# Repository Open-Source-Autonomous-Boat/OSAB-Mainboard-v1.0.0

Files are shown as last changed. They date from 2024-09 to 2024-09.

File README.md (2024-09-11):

# OSAB-Mainboard-v1.0.0
Mainboard for navigation and control of the vessel. Based on the RP2040. This is a prototype design that is not polished or suitable for use by others. It has been made freely available for educational and historical reasons only.

> ***NOTE:* V1.0.0 IS A PROTOTYPE VERSION. It is not recommended for ANY use. V1.0.0 is the only iteration in the V1.x.x series.**

### Features
- RP2040 processor (16MB flash)
- USB-C power and data connector
- SWD debugging port
- Boot select and reset button
- LiPo/Li-Ion backup battery with charger
- Red power indicator LED
- Yellow battery charge indicator LED
- Three blue LEDs (User-programmable, located in a line for optional use as a 3-bit binary status/error code output)
- Two WS2812B RGB LEDs (User-programmable)
- 4x DIP switch array for input (User-programmable)
- E-STOP button connector (JST-PH)
- Leak sensor connectors (two channels, two inputs per channel, JST-PH)
- GPS (PA1616D)
- CR1220 coin cell holder for GPS (retains sat. positions and speeds up reboot)
- LoRa (RFM95CW)
- Connector for Adafruit BNO085 accelerometer/gyro/magnetometer module (JST-SH)
- SD card slot for mission files and data logging
- PWM servo and ESC output (JST-PH)
- CAN-Bus and 12v input (JST-PH)
- MCP25625 CAN-Bus controller/transceiver
- Two MPM3610 buck converters (12v to 5v and 3.3v)
- AP2112K linear voltage regulator for USB input (5v to 3.3v)

### Notes
- LoRa and CAN-Bus controller share SPI1
- Mounting holes don't fit M3 screws, but should fit M2.5 or M2
- DOUBLE CHECK THAT YOUR LiPo/Li-Ion BATTERY HAS BEEN WIRED WITH THE CORRECT POLARITY BEFORE CONNECTING
- Changing the value of R6 sets the charging current for the backup battery (10k = 100mA, 5k = 200mA, 2k = 500mA, 1k = 1000mA)

### Known Issues
- I2C pullup resistors for the BNO085 connector are series resistors, not pullup resistors (oops)
- Diode on the boot select button serves no purpose (originally intended to allow the button to serve as a user-programmable button after bootup, but was not connected due to a lack of available GPIO)

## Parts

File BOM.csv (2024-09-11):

ID | Name | Designator | Footprint | Quantity | Manufacturer Part | Manufacturer | Supplier | Supplier Part | Price
1 | CR1220-2 | B1 | BAT-SMD_CR1220-2 | 1 | CR1220-2 | Q&J | LCSC | C70381 | 0.217
2 | 10uF | C1,C4,C18,C20,C23,C26,C33 | C0603 | 7 | CSA0603X5R106M6R3JT | HRE(芯声) | LCSC | C3015157 | 0.005
3 | 27pF | C2,C3,C28,C29 | C0402 | 4 | GJM1555C1H270JB01D | muRata(村田) | LCSC | C88884 | 0.014
4 | 100nF | C5,C6,C7,C9,C11,C12,C13,C14,C15,C16,C19,C21,C24,C25,C30 | C0402 | 15 | GCM155R71C104KA55D | muRata(村田) | LCSC | C85857 | 0.003
5 | 1uF | C8,C10 | C0402 | 2 | TCC0402X5R105K100AT | CCTC(三环) | LCSC | C380293 | 0.002
6 | 22uF | C22,C27 | C0603 | 2 | CL10A226MQ8NRNC | SAMSUNG(三星) | LCSC | C59461 | 0.008
7 | 47pF | C31,C32 | C0603 | 2 | CL10C470JB8NNNC | SAMSUNG(三星) | LCSC | C1671 | 0.004
8 | S2B-PH-SM4-TB(LF)(SN) | CN1,CN2,CN5,CN6,CN7,CN8 | CONN-SMD_P2.00_S2B-PH-SM4-TB-LF-SN | 6 | S2B-PH-SM4-TB(LF)(SN) | JST | LCSC | C295747 | 0.167
9 | PH2.0-3PWB Horizontal | CN3,CN4 | CONN-TH_PH-3PWB | 2 | PH-3P卧贴 | BOOMELE(博穆精密) | LCSC | C81626 | 0.064
10 | BM03B-SRSS-TBT(LF)(SN) | CN11 | CONN-SMD_BM03B-SRSS-TBT-LF-SN | 1 | BM03B-SRSS-TBT(LF)(SN) | JST | LCSC | C495538 | 0.279
11 | SM04B-SRSS-TB (LF)(SN) | CN12 | CONN-SMD_4P-P1.00_SM04B-SRSS-TB-LF-SN | 1 | SM04B-SRSS-TB(LF)(SN) | JST | LCSC | C160404 | 0.161
12 | MBR0540 | D1,D3,D4,D5,D6 | SOD-123FL_L2.7-W1.8-LS3.8-RD | 5 | MBR0540 | SHIKUES(时科) | LCSC | C116159 | 0.017
13 | NSR0320MW2T1G | D2 | SOD-323_L1.8-W1.3-LS2.5-RD | 1 | NSR0320MW2T1G | onsemi(安森美) | LCSC | C48192 | 0.052
14 | HL-PSC-2012U36FC | LED1,LED8 | LED0805-RD_RED | 2 | HL-PSC-2012U36FC | HONGLITRONIC(鸿利光电) | LCSC | C497949 | 0.076
15 | E6C0805UYAC1UDA | LED2 | LED0805-R-RD | 1 | E6C0805UYAC1UDA | ekinglux(亿晶源) | LCSC | C375452 | 0.02
16 | HL-PC-2012H392BC-L | LED3,LED4,LED5 | LED0805-RD_BLUE | 3 | HL-PC-2012H392BC-L | HONGLITRONIC(鸿利光电) | LCSC | C497943 | 0.014
17 | WS2812B-B/W | LED6,LED7 | LED-SMD_4P-L5.0-W5.0-TL_WS2812B-B | 2 | WS2812B-B/T | worldsemi | LCSC | C2761795 | 0.076
18 | DMP2045U-7 | Q1 | SOT-23-3_L2.9-W1.3-P1.90-LS2.4-BR-CW | 1 | DMP2045U-7 | DIODES(美台) | LCSC | C459541 | 0.078
19 | 1kΩ | R1,R5,R16,R17,R26 | R0603 | 5 | 0603WAF1001T5E | UNI-ROYAL(厚声) | LCSC | C21190 | 0.001
20 | 10kΩ | R2,R10,R11,R13,R14,R15,R20,R21,R29,R30,R31 | R0603 | 11 | FRC0603F1002TS | FOJAN(富捷) | LCSC | C2906982 | 0.001
21 | 27Ω | R3,R4 | R0402 | 2 | 0402WGJ0270TCE | UNI-ROYAL(厚声) | LCSC | C25156
22 | 5.1kΩ | R6,R9,R12 | R0603 | 3 | ARG03DTC5101 | Viking(光颉) | LCSC | C311919 | 0.007
23 | 10kΩ | R7 | R0603 | 1 | 0603WAF1002T5E | UNI-ROYAL(厚声) | LCSC | C25804 | 0.001
24 | 24kΩ | R8 | R0603 | 1 | 0603WAF2402T5E | UNI-ROYAL(厚声) | LCSC | C23352 | 0.001
25 | 75kΩ | R18 | R0603 | 1 | 0603WAF7502T5E | UNI-ROYAL(厚声) | LCSC | C23242 | 0.001
26 | 100kΩ | R19,R24,R25,R27,R28 | R0603 | 5 | 0603WAF1003T5E | UNI-ROYAL(厚声) | LCSC | C25803 | 0.001
27 | 120kΩ | R22 | R0603 | 1 | 0603WAF1203T5E | UNI-ROYAL(厚声) | LCSC | C25808 | 0.001
28 | 19.1kΩ | R23 | R0603 | 1 | RMC060319.1K1%N | Tyohm(幸亚电阻) | LCSC | C269469 | 0.003
29 | 1040310811 | SIM1 | SIM-SMD_8P-1040310811 | 1 | 1040310811 | MOLEX | LCSC | C585350 | 0.671
30 | KMR241GLFS | SW1,SW2 | KEY-SMD_4P-L4.2-W2.8-P1.60-LS4.6 | 2 | KMR241GLFS | C&K | LCSC | C221682 | 0.646
31 | RP2040 | U1 | LQFN-56_L7.0-W7.0-P0.4-EP | 1 | RP2040 | Raspberry Pi(树莓派) | LCSC | C2040 | 1.052
32 | W25Q64JVXGIQ | U2 | XSON-8_L4.0-W4.0-P0.80-TL-EP | 1 | W25Q64JVXGIQ | WINBOND(华邦) | LCSC | C2940195 | 0.641
33 | AP2112K-3.3TRG1 | U3 | SOT-25-5_L3.0-W1.8-P0.95-LS3.0-BR | 1 | AP2112K-3.3TRG1 | DIODES | LCSC | C51118 | 0.083
34 | MCP73831T-2ATI/OT | U4 | SOT-23-5_L3.0-W1.7-P0.95-LS2.8-BR | 1 | MCP73831T-2ATI/OT | MICROCHIP(美国微芯) | LCSC | C14879 | 0.93
35 | MPM3610GQV-Z | U5,U15 | QFN-20_L5.0-W3.0-TL-MPM3610GQV-Z | 2 | MPM3610GQV-Z | MPS(芯源) | LCSC | C5183856 | 2.914
36 | S5B-PH-SM4-TB(LF)(SN) | U6 | CONN-SMD_S5B-PH-SM4-TB-LF-SN | 1 | S5B-PH-SM4-TB(LF)(SN) | JST | LCSC | C265104 | 0.191
37 | PA1616D GPS module | U8 | PA1616D GPS MODULE | 1
38 | RFM95CW | U9 | RFM95CW | 1 | RFM95CW | Hoperf | Digi-Key | RFM95CW
39 | MCP25625-E/ML | U10 | QFN-28_L6.0-W6.0-P0.65-BL-EP | 1 | MCP25625-E/ML | MICROCHIP(美国微芯) | LCSC | C481365 | 2.118
40 | CFS-0402TA | U11 | SW-SMD_8P-L11.1-W6.2-P2.54-LS7.8 | 1 | CFS-0402TA | NIDEC(尼得科) | LCSC | C2921586 | 0.823
41 | TYPE-C-31-M-12 | USBC1 | USB-C_SMD-TYPE-C-31-M-12 | 1 | TYPE-C-31-M-12 | Rectangular Connectors - Contacts | LCSC | C165948 | 0.161
42 | 12MHz | X1,X2 | CRYSTAL-SMD_4P-L3.2-W2.5-BL | 2 | NX3225SA-12MHz-STD-CSR-6 | NDK | LCSC | C481400 | 0.424
43 | U.FL-R-SMT-1(40) | RF1,RF2 | ANT-SMD_UFL-R-SMT-1 | 2 | U.FL-R-SMT-1(40) | HRS(广濑) | LCSC | C434816 | 1.371

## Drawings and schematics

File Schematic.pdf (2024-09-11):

## USB Power

## Power

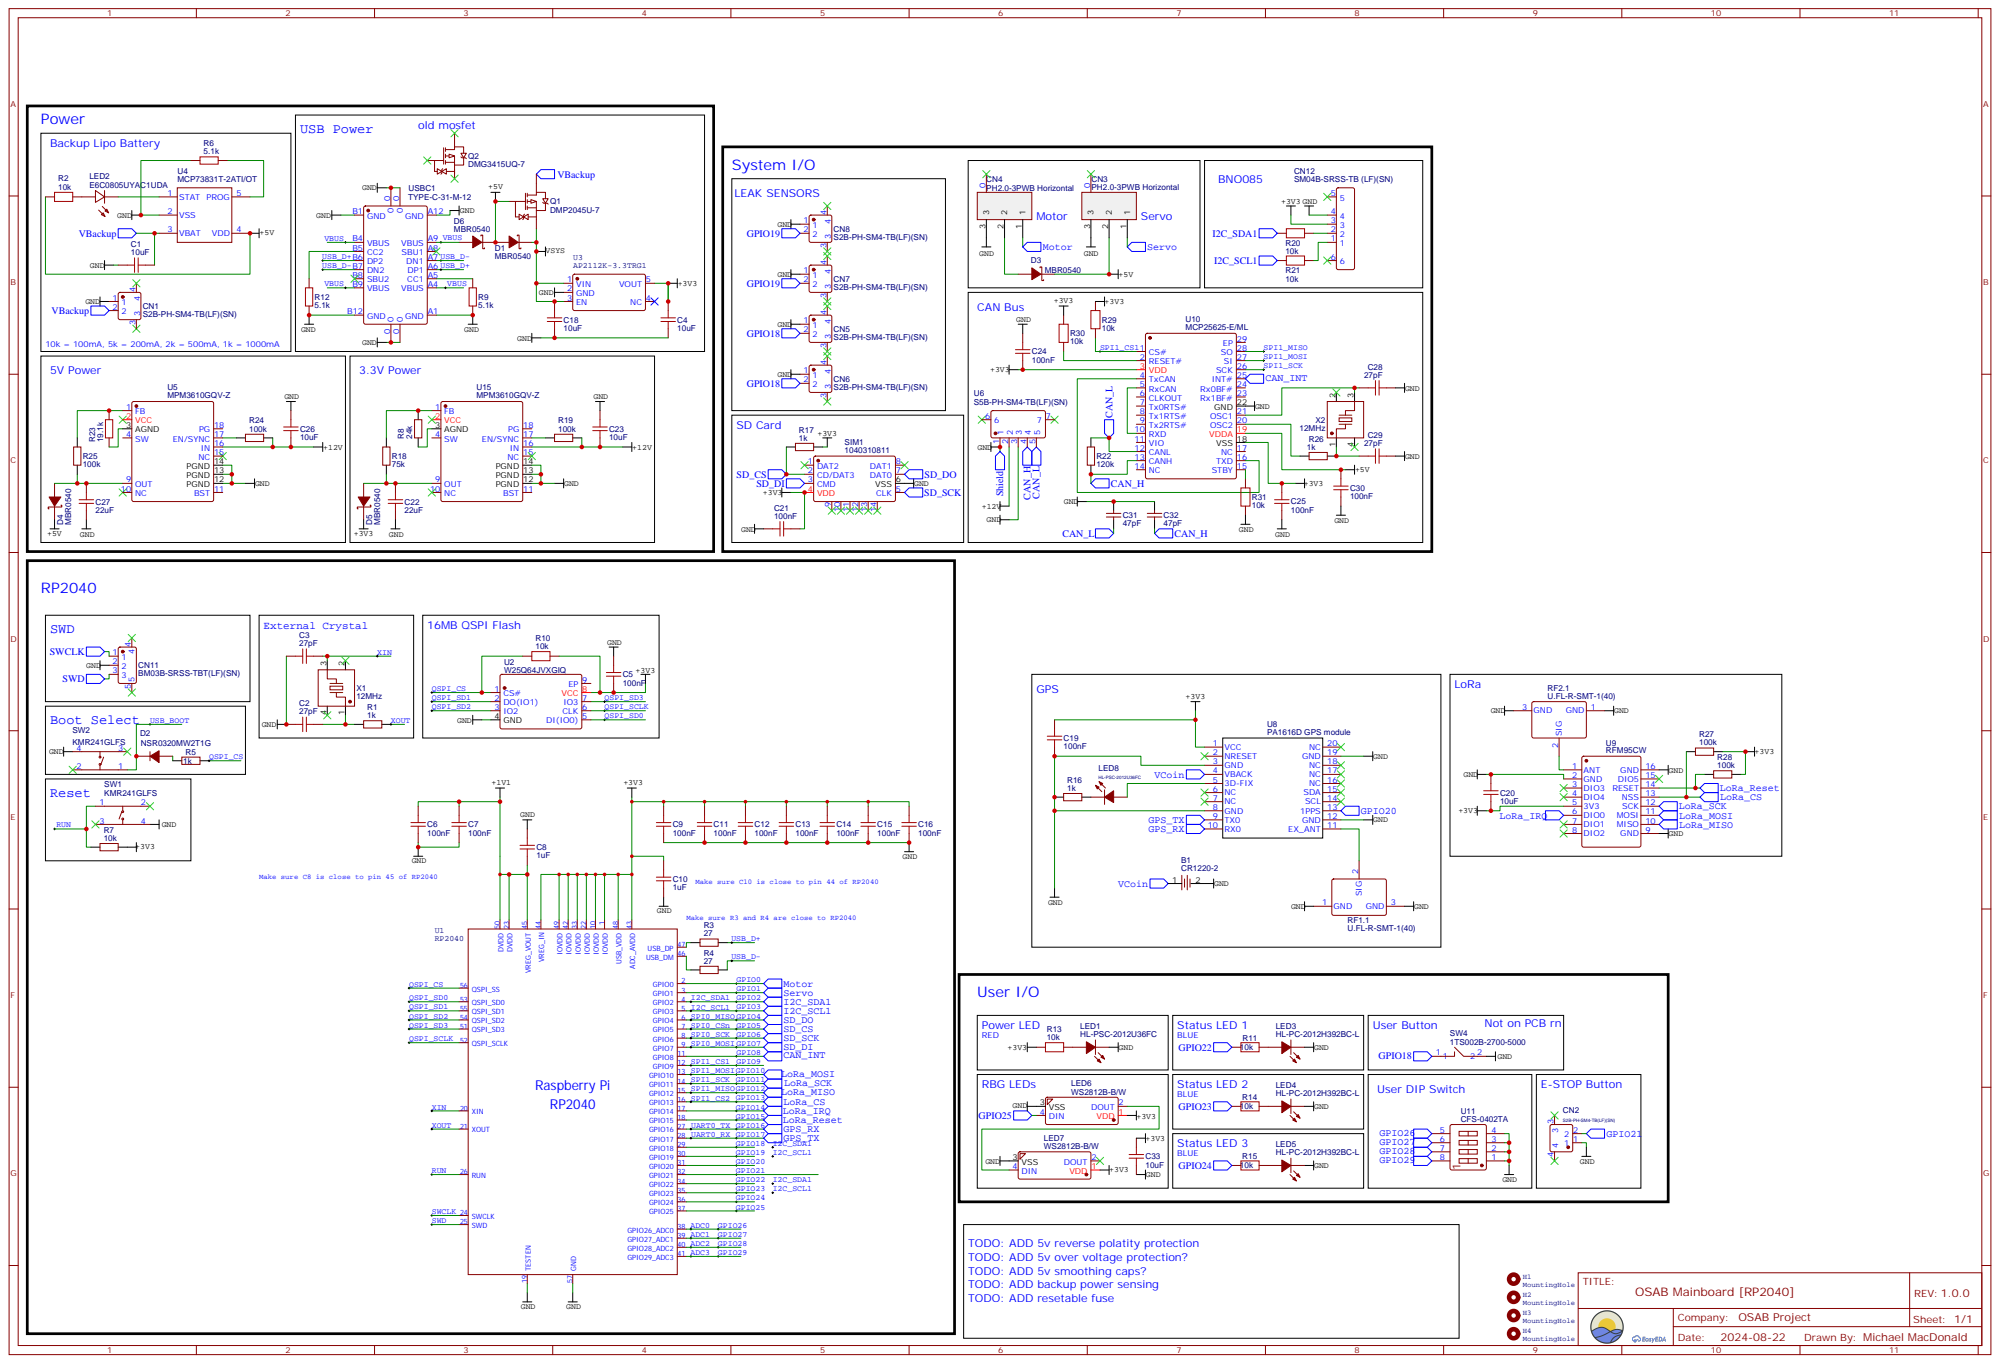
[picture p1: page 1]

Make sure C8 is close to pin 45 of RP2040

Make sure C10 is close to pin 44 of RP2040

Not on PCB rn

TODO: ADD 5v reverse polatity protection
TODO: ADD 5v over voltage protection?
TODO: ADD 5v smoothing caps?
TODO: ADD backup power sensing
TODO: ADD resetable fuse

Drawn By: Michael MacDonald

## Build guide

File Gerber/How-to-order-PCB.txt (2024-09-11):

How to Order PCB

Please refer to:
https://docs.easyeda.com/en/PCB/Order-PCB
